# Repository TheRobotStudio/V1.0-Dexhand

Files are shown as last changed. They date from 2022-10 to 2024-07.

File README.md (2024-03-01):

# V1.0-Dexhand

As a naming convention the forearm parts consist of a bulk, a split, inserts and shells - the stl files are in the Forearm folder.

The bulk is typically the larger of the forearm prints and houses the servos and other components.

The split is typically smaller and is effectively a lid though may also incorporate structural supports for components and other print inserts inside the forearm.

Inserts are detachable pieces necessary to assemble pieces inside the structure beneath other components.

Shells are thin coverings that cover over openings in the main structure.

Print all the files in the Forearm folder to make the forearm. The battery cover is optional and in practice the bulk shell seals all the components adequately if well printed.

Some minor updates still required to finalise the tendon routing in the forearm and hand.

There are two main forearm structure files, Bulk and Split and additionally two shells, one to cover the servos in the palm and a pair to cover the outside of the forearm and seal over the electronics and battery compartment.

The Split print has mounting holes for the battery springs and an external hole to mount a 16mm latching push button switch to turn the hand on and off.

To download the stl files click the green button above on the right to drop down the Code menu. At the bottom click Download Zip.

The hand is made entirely by 3dprinting with additional total cost of components required for the hand around $300 USD.

The cad for the arm and hand is freely and publically available down to a parasolid level at:

https://cad.onshape.com/documents/16c809d35214bd31c5b0324f/w/56b2fb82f7bdce505771766f/e/df78e66574dc7dbd45e4826c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

The forearm and hand can operate as a stand-alone unit allowing unlimited axial rotation for rotational tasks like scrubbing.

Some notes on printing:

The parts can be printed on any extrusion printer and the hand uses less than 300 USD of components.

The parasolid CAD model can also be viewed and downloaded for free on the cloud platform Onshape: https://cad.onshape.com/documents/16c809d35214bd31c5b0324f/w/56b2fb82f7bdce505771766f/e/df78e66574dc7dbd45e4826c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

Designed and tested for high speed printing using a 0.6mm diameter nozzle and 0.4mm layer thickness except for the tendon spools which benefit from printing at 0.3mm layer thickness or better.

Tested in PLA, PETG and CF nylon. ABS is not recommended for the large pieces due to warping.

To finish 3d prints to a high standard requires a fine sandpaper or emery board.

Diamond coated steel nail files are a handy tool: https://amzn.to/3VBBsOX

Though my favourite diamond file is actually intended for maintaining whetstones, just a nice big expanse of diamond dust to use :-)

- Amazon US: https://amzn.to/3eN3bvo

Additional components required are listed below.

Please consider buying via the Amazon links where available to help fund the robot development.

The biggest cost item are the 16 slim micro-servos that drive the fingers and thumb.

The discount code ROBOTSERVOS will take off 10% from the official Emax webstore: https://emaxmodel.com

There are four variants at this size with plastic or metal gears and using either digital or analog control technology.

ES3301 (approx $6.6)
ES3302 (approx $9.2)
ES3351  (approx $8.5)
ES3352 (approx $12)

2 standard micro servos are needed for wrist flexion and extension.

Feetech SCS2332 - https://feetechrc.com/product-name_55300.html are recommended.

These are serial bus driven servos over allowing a greater range of controlled rotation.

They cost around 35 bucks each plus delivery.

If you prefer to use a standard PWM servo for simplicity they can be substituted by any servo that fits inside the envelope 23.2*12.1*28.5mm.

The trade off is the reduction of the powered range of motion of the wrist to about half.

1 standard servo needed for axial wrist rotation (optional)
Feetech SCS15 - https://feetechrc.com/6v-15kg-digital-robot-steering-gear.html or any servo that fits inside the envelope 40*20*40.5mm.

Reduces powered range of motion to about half and the loss of a continuous rotation option.

The rest of the components are relatively inexpensive:

2mm diameter steel pins - alternatively cut lengths from a wire coat hanger or in Europe order direct from https://www.visseriefixations.fr/goupilles/goupille-cylindrique-rectifiee-m6.html

Otherwise kits are available on Amazon US: https://amzn.to/3VYrnfh

M2 screw and washer kits, or also in Europe from https://www.visseriefixations.fr
Amazon US: https://amzn.to/3sf4NkE

M2 brass threaded inserts M2 * 4mm long * 3.5mm
Note that the type required has a plain section between the knurled ends to allow attachment of the tendon in the fingertip.
Amazon US: https://amzn.to/3yYl1lY

Kite or fishing line for finger tendons - Sufix 832 is the best I know of for longevity, the 80lbs breaking strength is stiff enough to thread easily and most readily available on 
Amazon US: https://amzn.to/3DgjNoF

Slightly thicker 0.8mm kiteline for the finger ligaments and wrist tendons.

Amazon US: https://amzn.to/3GMKQJL

Ball Bearings 6*10*3 - Need 50 for a hand, packs of 10 available which are enough for the sample finger.
Amazon US: https://amzn.to/3Dj7cBn

Ball Bearings 2*6*3 or 2*6*2.5 - Need 6 for the wrist
Amazon US: https://amzn.to/3yYlTHg

Ball Bearings 15*21*4 - Need 4 for the wrist
Amazon US: https://amzn.to/3TsMSTO

Ball Bearings 3*8*4 - Need 6 for the wrist
Amazon US: https://amzn.to/3VyE28O

M3 * 70mm caphead bolt (grade 12.9 ideally)
Need 2 (1 is cut down to 60mm)
Amazon US: https://amzn.to/3HM0Rjx
McMaster US: https://www.mcmaster.com/product/91290A297

Follow @therobotstudio
Get involved at patreon.com/therobotstudio

Shield: [][cc-by-nc-sa]

This work is licensed under a
[Creative Commons Attribution-NonCommercial-ShareAlike 4.0 International License][cc-by-nc-sa].

[][cc-by-nc-sa]

[cc-by-nc-sa]: http://creativecommons.org/licenses/by-nc-sa/4.0/
[cc-by-nc-sa-image]: https://licensebuttons.net/l/by-nc-sa/4.0/88x31.png
[cc-by-nc-sa-shield]: https://img.shields.io/badge/License-CC%20BY--NC--SA%204.0-lightgrey.svg

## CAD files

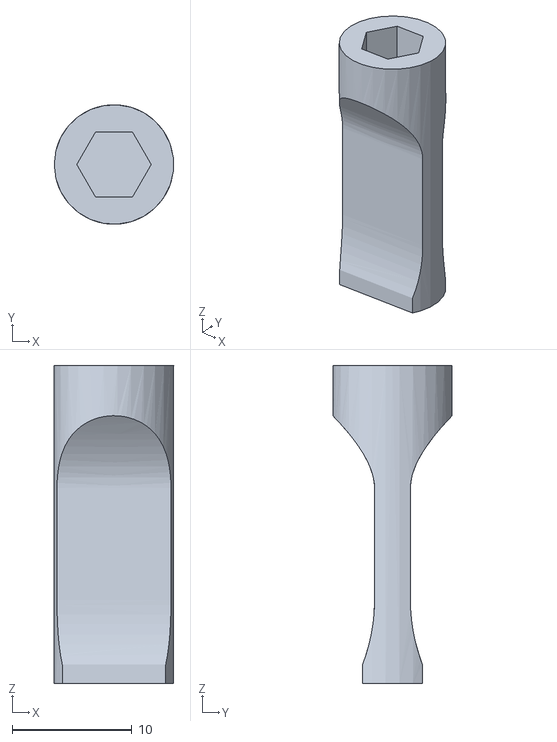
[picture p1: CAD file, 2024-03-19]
Forearm/M3_Socket_02.STL
10.0 x 10.00 x 26.6

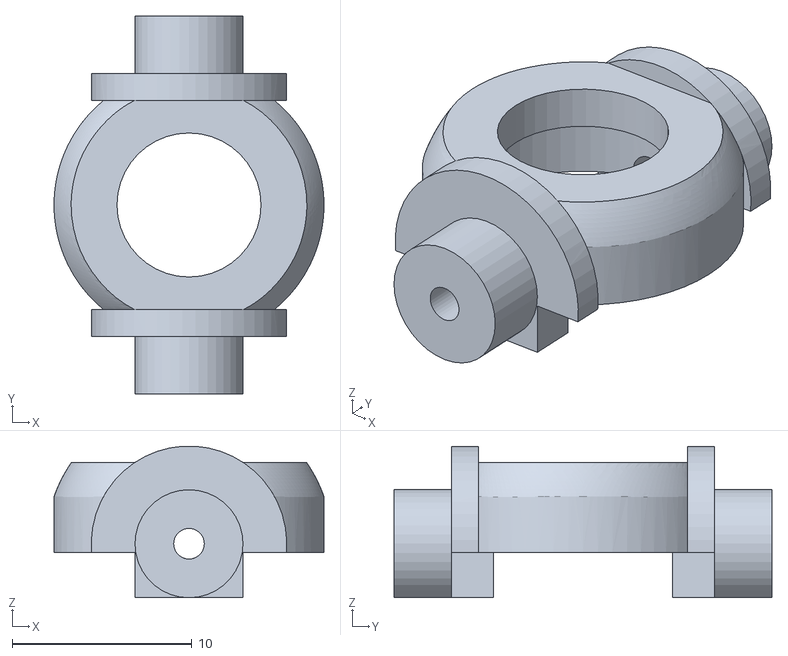
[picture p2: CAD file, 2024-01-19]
Hand_06/CMC_Yaw_15a.STL
15.0 x 21.0 x 8.42

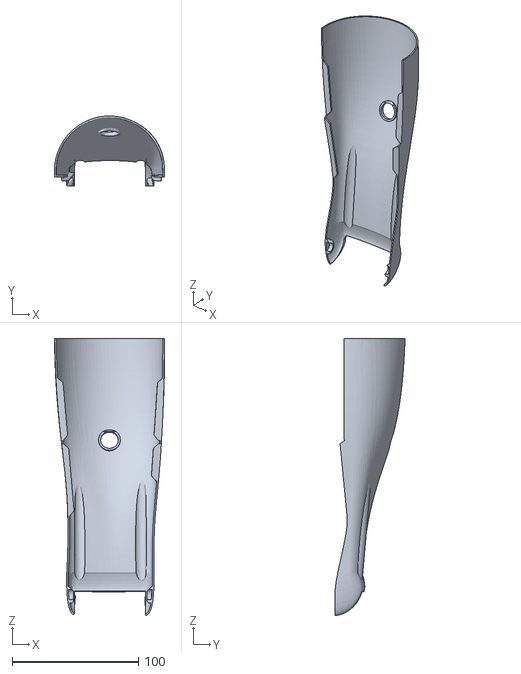
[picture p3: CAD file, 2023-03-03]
Patreon_Forearm_Shells/Forearm_Duplex_Wrist_19c_Jessie_02_Left_Split_Cover.STL
87.4 x 55.6 x 219.6

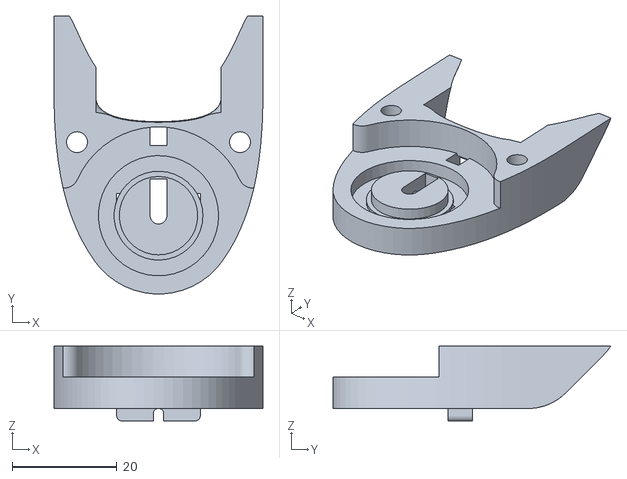
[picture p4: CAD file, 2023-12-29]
Wrist_10/Proximal_Wrist_10a_5mm_Holes.STL
40.0 x 53.2 x 14.4

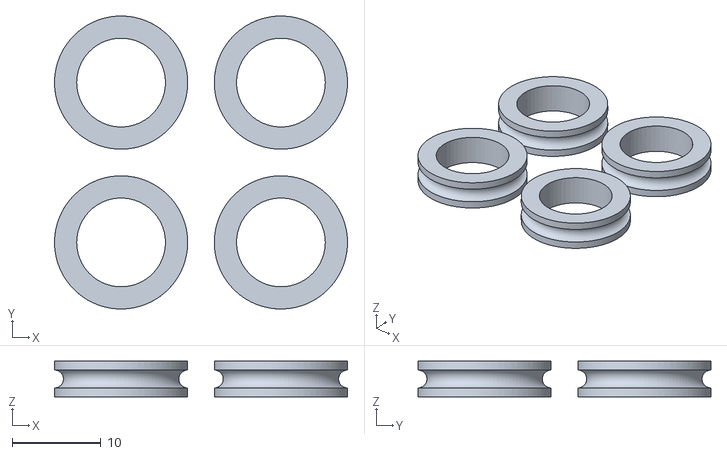
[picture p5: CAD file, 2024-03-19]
Forearm/10_15_4.STL
33.0 x 33.0 x 4.00

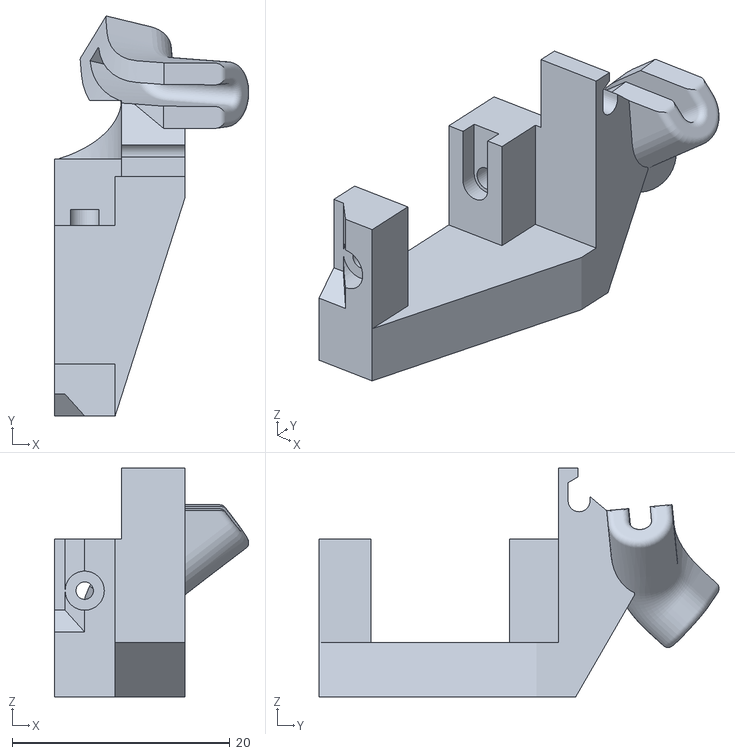
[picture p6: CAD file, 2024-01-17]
Hand_06/Thumb_Tendon_Hanger_03a.STL
17.9 x 36.8 x 21.0

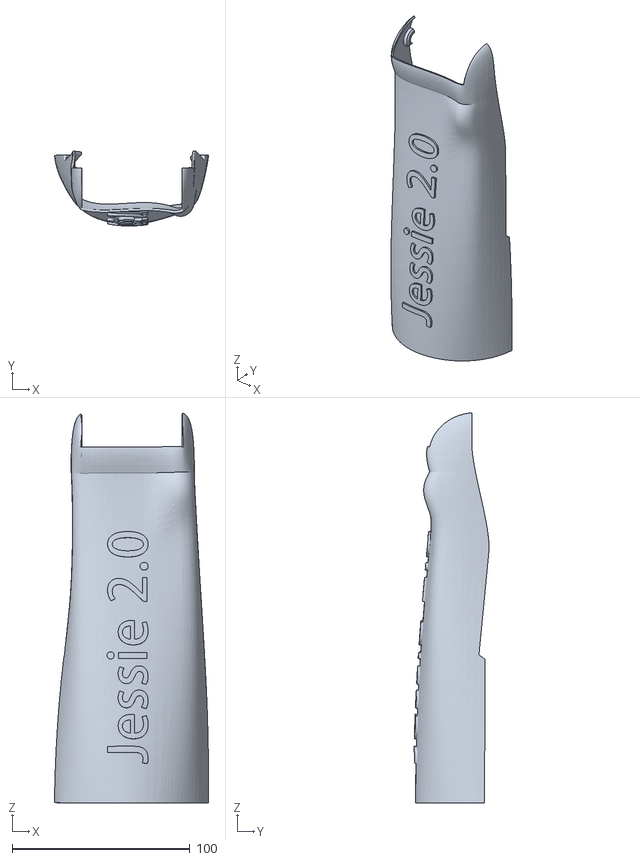
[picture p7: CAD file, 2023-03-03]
Patreon_Forearm_Shells/Forearm_Duplex_Wrist_19c_Jessie_02_Right_Bulk_Cover.STL
86.9 x 42.3 x 219.7

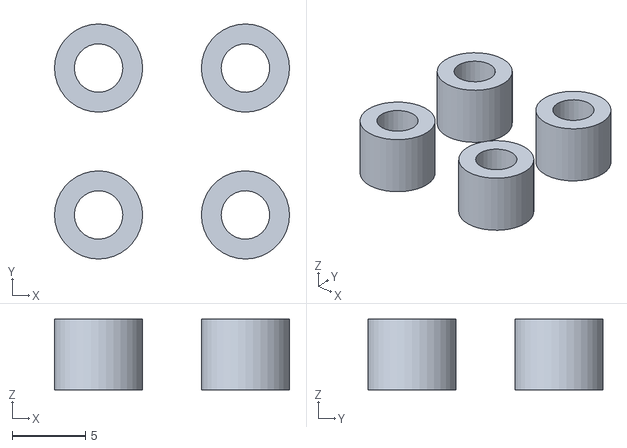
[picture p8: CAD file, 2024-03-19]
Forearm/Wrist_Pulley_Centres_03.STL
16.0 x 16.0 x 4.80

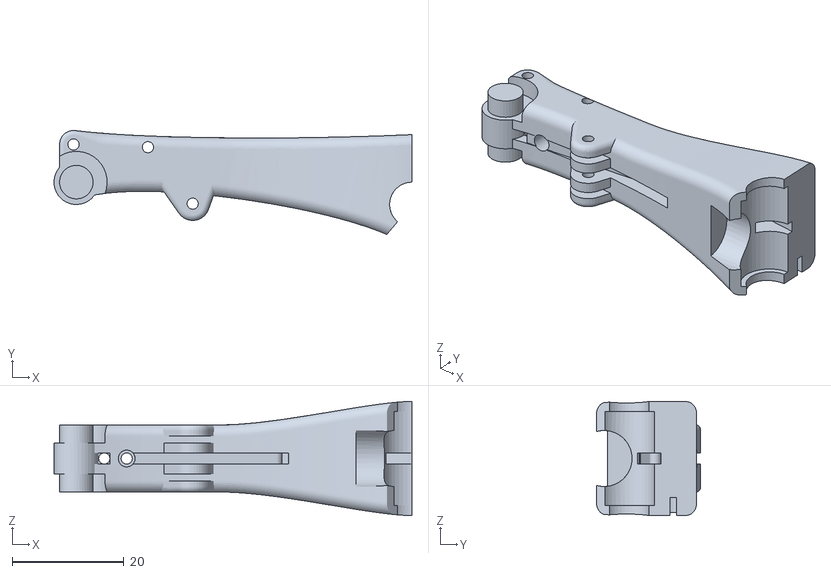
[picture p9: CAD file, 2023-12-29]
Hand_06/PLP_THUMB_15b.STL
64.0 x 18.6 x 20.4

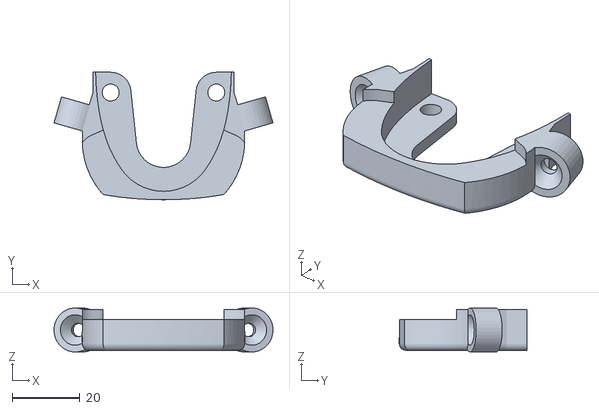
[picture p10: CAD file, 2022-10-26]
Wrist_10/Proximal_Wrist_10_Tendon_Hanger_5mm_Holes.STL
64.7 x 37.7 x 13.0

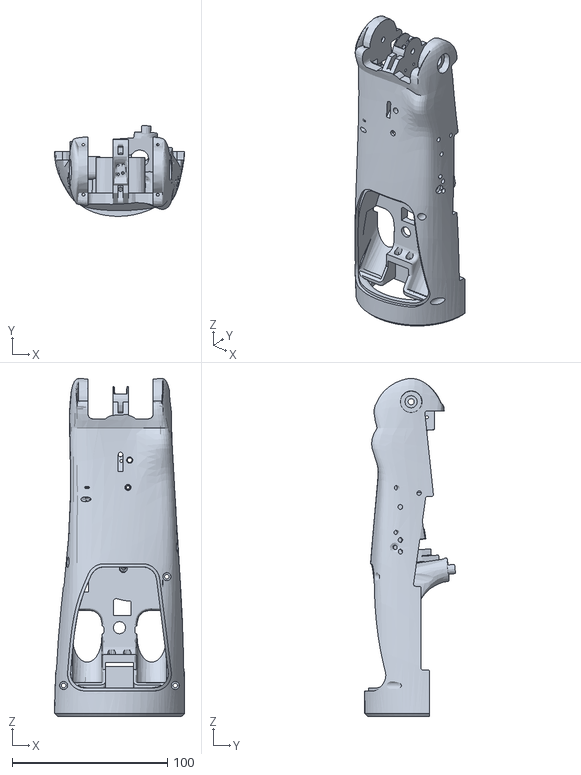
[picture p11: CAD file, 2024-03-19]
Forearm/Forearm_Duplex_Wrist_17j_Bulk.STL
84.0 x 58.5 x 218.0

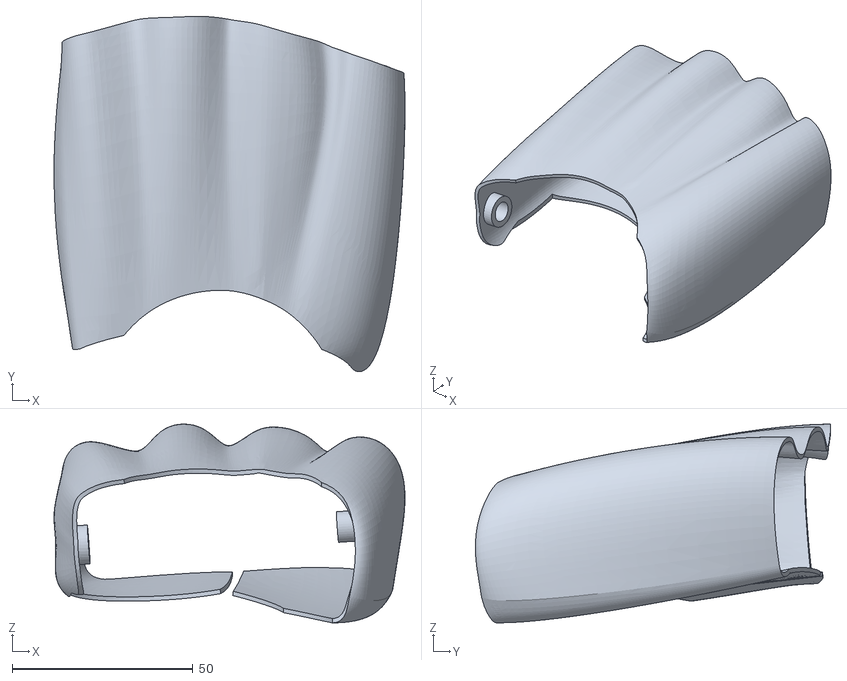
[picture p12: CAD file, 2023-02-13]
Hand_06/Back_of_Hand_23a.STL
97.1 x 98.3 x 55.0

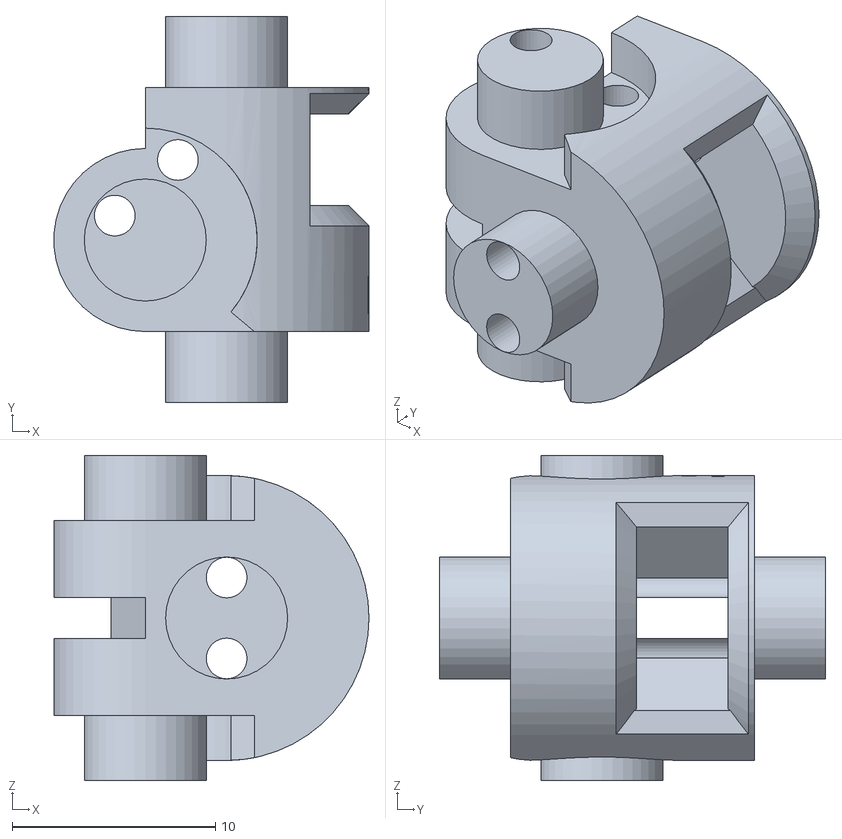
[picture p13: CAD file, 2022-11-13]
Hand_06/Knuckle_15.STL
15.5 x 19.0 x 16.0

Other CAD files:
Wrist_10/Proximal_Wrist_10a_4mm_Holes.STL
Patreon_Forearm_Shells/Forearm_Duplex_Wrist_19c_Jessie_02_Left_Bulk_Cover.STL
Patreon_Forearm_Shells/Forearm_Duplex_Wrist_19c_Jessie_02_Right_Split_Cover.STL
Wrist_10/Proximal_Wrist_10_Tendon_Hanger_4mm_Holes.STL
Forearm/Forearm_Duplex_Wrist_19c_TRS_01_Split_Cover.STL
Forearm/Forearm_Duplex_Wrist_18c_Insert_01.STL
Forearm/Forearm_Duplex_Wrist_18c_Insert_02.STL
Forearm/Forearm_Duplex_Wrist_18c_Insert_03.STL
Forearm/Forearm_Duplex_Wrist_18d_Battery_Cover.STL
Forearm/Forearm_Duplex_Wrist_18i_Split_a.STL
Forearm/Forearm_Duplex_Wrist_19c_TRS_01_Bulk_Cover.STL
Hand_06/CMC_Pitch_15.STL
Hand_06/MLP_100_15.STL
Hand_06/MLP_105_15.STL
Hand_06/MLP_90_15.STL
Hand_06/MLP_THUMB_15.STL
Hand_06/PLP_100_15.STL
Hand_06/PLP_105_15.STL
Hand_06/PLP_90_15.STL
Hand_06/Palm_Fore_Bulk_15.STL
Hand_06/Palm_Fore_Split_15.STL
Hand_06/Palm_Little_Bulk_15.STL
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

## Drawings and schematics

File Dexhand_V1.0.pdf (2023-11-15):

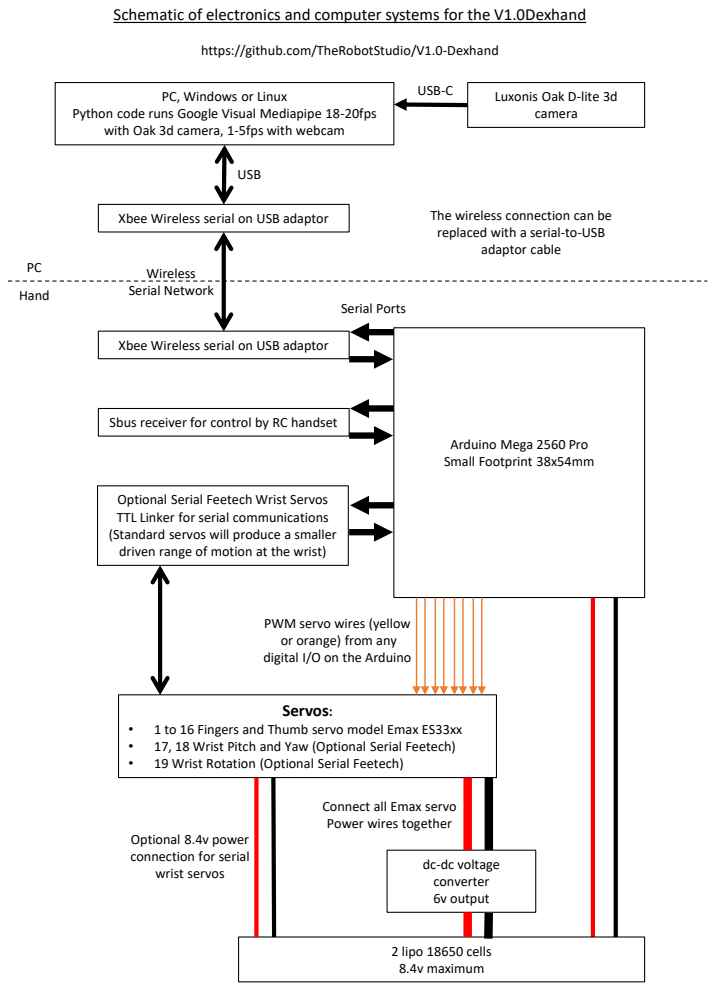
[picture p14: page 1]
Servos:; USB; Wireless Serial Network; Serial Ports; adaptor cable; USB-C; 2 lipo 18650 cells 8.4v maximum; Hand

Schematic of electronics and computer systems for the V1.0Dexhand

https://github.com/TheRobotStudio/V1.0-Dexhand

PC, Windows or Linux

Luxonis Oak D-lite 3d
camera

Python code runs Google Visual Mediapipe 18-20fps
with Oak 3d camera, 1-5fps with webcam

The wireless connection can be
replaced with a serial-to-USB

Xbee Wireless serial on USB adaptor

Sbus receiver for control by RC handset

Arduino Mega 2560 Pro
Small Footprint 38x54mm

Optional Serial Feetech Wrist Servos
TTL Linker for serial communications
(Standard servos will produce a smaller
driven range of motion at the wrist)

PWM servo wires (yellow
or orange) from any
digital I/O on the Arduino

• 1 to 16 Fingers and Thumb servo model Emax ES33xx
• 17, 18 Wrist Pitch and Yaw (Optional Serial Feetech)
• 19 Wrist Rotation (Optional Serial Feetech)

Connect all Emax servo
Power wires together

Optional 8.4v power
connection for serial
wrist servos

dc-dc voltage
converter
6v output

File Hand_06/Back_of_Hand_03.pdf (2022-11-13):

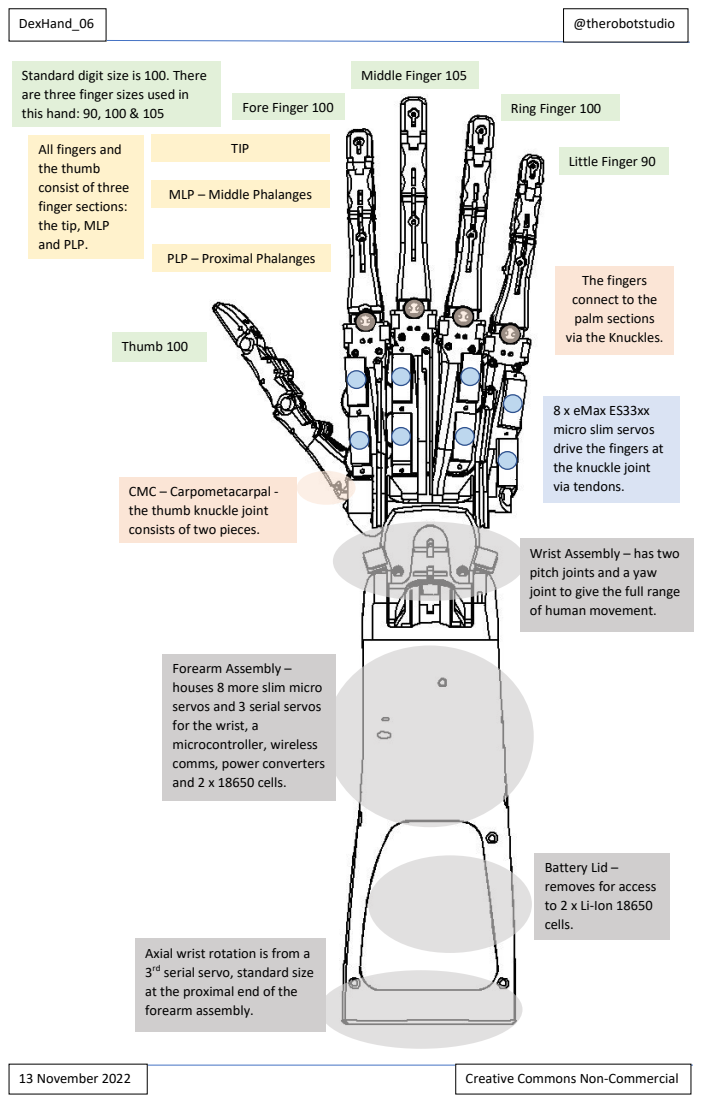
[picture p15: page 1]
DexHand_06; @therobotstudio; 13 November 2022; Creative Commons Non-Commercial; Little Finger 90; Ring Finger 100; Middle Finger 105; Fore Finger 100; Thumb 100; TIP

Standard digit size is 100. There
are three finger sizes used in
this hand: 90, 100 & 105

All fingers and
the thumb
consist of three
finger sections:
the tip, MLP
and PLP.

MLP – Middle Phalanges

PLP – Proximal Phalanges

The fingers
connect to the
palm sections
via the Knuckles.

8 x eMax ES33xx
micro slim servos
drive the fingers at
the knuckle joint

via tendons. CMC – Carpometacarpal -

the thumb knuckle joint consists of two pieces.

Wrist Assembly – has two pitch joints and a yaw joint to give the full range of human movement.

Forearm Assembly –
houses 8 more slim micro
servos and 3 serial servos
for the wrist, a
microcontroller, wireless
comms, power converters
and 2 x 18650 cells.

Battery Lid – removes for access to 2 x Li-Ion 18650 cells.

Axial wrist rotation is from a 3 rd serial servo, standard size at the proximal end of the forearm assembly.

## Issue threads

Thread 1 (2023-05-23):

BOM - Missing Some Bearing Sizes

tshumay, 2023-05-23:
Reminder to add bearing sizes for the bearings that go between the 70mm M3 Bolt and Bulks.

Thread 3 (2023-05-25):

BOM - Mating Connector for M3 Countersunk Screws in Wrist

tshumay, 2023-05-25:
Currently unclear what kind of flush connector to use for M3 countersunk screws - heat sink? Sleeve nut?

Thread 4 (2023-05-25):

Geometry - Thumb heat-sink insert not in right place.

tshumay, 2023-05-25:
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

I believe this bore may be in the wrong place if it is intended to accept the heat-set insert from the top of the thumb

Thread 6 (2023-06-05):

Unclear Which Shells Fit Together

tshumay, 2023-06-05:
I'm not sure if there's a matching top/bottom shell set in the STL files. I printed the Forearm_Duplex_Wrist17f_Bulk forearm as my basis, but none of the top shells seem to fit. I started with Forearm_Duplex_Wrist_18i_Split, but there is a gap. And the others seem to not fit  in CAD.

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

TheRobotStudio, 2023-06-06:
Yes that’s right, the gap allows the cosmetic shells to clip on!On the V2 it’s neater 😁Sent from my iPhoneOn 5 Jun 2023, at 22:43, Trent Shumay ***@***.***> wrote:
I'm not sure if there's a matching top/bottom shell set in the STL files. I printed the Forearm_Duplex_Wrist17f_Bulk forearm as my basis, but none of the top shells seem to fit. I started with Forearm_Duplex_Wrist_18i_Split, but there is a gap. And the others seem to not fit  in CAD.

—Reply to this email directly, view it on GitHub, or unsubscribe.You are receiving this because you are subscribed to this thread.Message ID: ***@***.***>

tshumay, 2023-06-06:
Ahhh! That makes sense. Thanks! I’ve got the right ones printed then. _____________________________Trenton ShumayCEO, IoT Design Shop Inc. On Jun 5, 2023, at 9:57 PM, TRS ***@***.***> wrote:
Yes that’s right, the gap allows the cosmetic shells to clip on!On the V2 it’s neater 😁Sent from my iPhoneOn 5 Jun 2023, at 22:43, Trent Shumay ***@***.***> wrote:
I'm not sure if there's a matching top/bottom shell set in the STL files. I printed the Forearm_Duplex_Wrist17f_Bulk forearm as my basis, but none of the top shells seem to fit. I started with Forearm_Duplex_Wrist_18i_Split, but there is a gap. And the others seem to not fit  in CAD.

—Reply to this email directly, view it on GitHub, or unsubscribe.You are receiving this because you are subscribed to this thread.Message ID: ***@***.***>

—Reply to this email directly, view it on GitHub, or unsubscribe.You are receiving this because you authored the thread.Message ID: ***@***.***>

Closed 2023-06-07.

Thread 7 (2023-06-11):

Geometry - Mechanical Interference

tshumay, 2023-06-11:
Especially with some deviation in 3D printing, there is a mechanical interference with the top right tendon port and the servo mounting positions on the forearm.

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

TheRobotStudio, 2023-07-23:
Yes - this is intended to be cleared with a 2mm drill prior to assembly!

tshumay, 2023-07-23:
It's not the hole itself, so much as the tendon being impeded by the servo body. I cleared the holes, but it's obscured by the mount tail of the servo.

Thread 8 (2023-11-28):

SG90 Alternative Micro Servo Model

ingochris, 2023-11-28:
```
Future iterations will be able to fit SC90 servos which are considerably cheaper.
```

Saw this on another platform (thing:5466653) but comments aren't pushing there for some reason.
I'm guessing your team meant SG90 micro servos.

My question is:
Was this ever integrated to the STL's and microcontroller code?

TheRobotStudio, 2023-11-28:
Hi,

I've yet to finish modifying the stl's but the code would be the same as SG90's and Emax ES33xx servos are both legacy PWM servos.

Cheers,

Rob

ingochris, 2023-11-29:
Thanks, looking forward to it! I have printer and SG90's ready to test once the model is updated.

TheRobotStudio, 2023-11-29:
There is a single finger example of you want to try now: https://www.thingiverse.com/thing:5384399Sent from my iPhoneOn 29 Nov 2023, at 02:50, Christopher Ngo ***@***.***> wrote:
Thanks, looking forward to it! I have printer and SG90's ready to test once the model is updated.

—Reply to this email directly, view it on GitHub, or unsubscribe.You are receiving this because you commented.Message ID: ***@***.***>

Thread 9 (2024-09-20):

1 finger fill missing

jahid0298, 2024-09-20:
I can see here 4 finger. One is missing

TheRobotStudio, 2024-09-21:
There are three fingers specified in the stl because the 1st finger and the 3rd finger are identical. The middle finger is 105% relative size and the little finger is 90%.

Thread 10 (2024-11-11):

Steering gear power supply

dadffaser, 2024-11-11:
I would like to know how the ten motors of the dexhand are controlled, how do you solve the power supply problem of so many motors

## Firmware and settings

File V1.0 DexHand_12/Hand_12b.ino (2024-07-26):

/*   Copyright 2021 Feetech RC Model CO.,LTD
 *
 *  Licensed under the Apache License, Version 2.0 (the "License");
 *  you may not use this file except in compliance with the License.
 *  You may obtain a copy of the License at
 *
 *       http://www.apache.org/licenses/LICENSE-2.0
 *
 *  Unless required by applicable law or agreed to in writing, software
 *  distributed under the License is distributed on an "AS IS" BASIS,
 *  WITHOUT WARRANTIES OR CONDITIONS OF ANY KIND, either express or implied.
 *  See the License for the specific language governing permissions and
 *  limitations under the License.

 Compared to Hand_12 the function of the serial ports 0 and 3 have been swapped over.
 This means that now the servos can be controlled without an additional USB to serial connection from the PC.
 The standard USB connection built into the Arduino mega will now read serial output from the PC.
 If an extra FTDI or CH340 USB to serial adaptor is available it can be connected to serial port 3 for debugging.

 On the mega Pin 14 is TxD connects to Yellow (FTDI) or White (CH340)
             Pin 15 is RxD connects to Orange (FTDI) or Green (CH340)

 For both types Red connects to +5v
                Black connects to Ground           

 */

 
#include "SBUS.h"
#include "Servo.h"
#include "SCServo.h"

// a SBUS object, which is on hardware
// serial port 1
SBUS x8r(Serial1);

Servo emaxservo_RTI;  // 26 RT I Ring Tendon Inverted, 27, 28, 29, 30, 31, 24, 48, 49, 50, 51, 52, 53, 45, 46, 47
Servo emaxservo_LTI;  // 27 LT I Little Tendon Inverted
Servo emaxservo_LON;  // 28 LO N Little Outward at Knuckle Non-Inverted
Servo emaxservo_LII;  // 29 LI I Little Inward at Knuckle Inverted
Servo emaxservo_ROI;  // 30 RO I Ring Outward
Servo emaxservo_RII;  // 31 RI Ring Inward
Servo emaxservo_TRN;  // 24 TR N Thumb Rotation Non-Inverted
Servo emaxservo_FTN;  // 48 FT N Fore Tendon Non
Servo emaxservo_MTN;  // 49 MT N Middle Tendon Non
Servo emaxservo_FII;  // 51 FI I Fore Inward Inverted
Servo emaxservo_FON;  // 50 FO N
Servo emaxservo_MON;  // 52 MO N
Servo emaxservo_MIN;  // 53 MI N
Servo emaxservo_TII;  // 45 TI I Thumb Inwards
Servo emaxservo_TTN;  // 46 TT N Thumb Tendon Non
Servo emaxservo_TON;  // 47 TO N Thumb Outwards Non



// twelve servo objects can be created on most boards.
//On the Mega, up to 12 servos can be used without interfering with PWM functionality; use of 12 to 23 motors will disable PWM on pins 11 and 12.

int pos[] ={0, 0, 0, 0,
            0, 0, 0, 0,
            0, 0, 0, 0,
            0, 0, 0, 0};    // variable to store positions


int servo_pos[] ={90, 90, 90, 90,       // variable to store the servo positions for four fingers (3 powered dof each) and thumb (4 powered dof)
                  90, 90, 90, 90,       // setting to zero causes little servo jump at start up
                  90, 90, 90, 90,
                  90, 90, 90, 90}; 

int wrist_pos[] = {512, 512, 512};     // default to centre

// channel, fail safe, and lost frames data
uint16_t channels[16];
bool failSafe;
bool lostFrame;

long default_counter = 1;
int default_stage = 0;


SCServo SERVO;      //Declare a case of SCServo to control the Feetechs

//
int analogPin0 = A0; // potentiometer wiper (middle terminal) connected to analog pin 0
                    // outside leads to ground and +5V
int analogPin1 = A1;  //Knuckle Yaw
int analogPin2 = A2;  //Sequence
                    
int val0 = 0;  // variable to store the value read
int val1 = 0;
int val2 = 0;
int a = 0;      //Print out angles
int b = 0;      //Servo limits for loop
int l = 0;      //for loop counter
int s = 511;      //sequence counter
bool Sense = 1;

int bytecount = 0;
int bus_start = 0;
int bus_end = 0;
int checksum = 0;
int angles[23] = {0};
byte lo;            //low byte of checksum int

int digi = 0;
int digitemp = 0;
int newmsg = 0;

int action = 0;
int prev_action = 0;

int ring_offset = 0;

//White Hand
//ID1: 380 570
//ID2: 0 1023
//ID3: 360 570
//ID4: 0 1023
//ID5: 450 640
//ID6: 0 1023 Neg
//ID7: 40 600
//ID8: 0 1023 Neg
//ID9: 400 800 Neg
//ID10: 0 1023
int Servo_Min[] = {0, 380, 0, 360, 0, 450, 0, 400, 0, 400, 0};
int Servo_Max[]= {0, 570, 1023, 570, 1023, 640, 1023, 600, 1023, 800, 1023};
int Mid_Point[10];

int wrist[2] = {512, 512};
int Servo_Order[]= {26, 27, 28, 29, 
                    30, 31, 24, 48,
                    49, 50, 51, 52,
                    53, 45, 46, 47};

void setup() {
  //The Mega and Due boards have 4 UART each
  //For the Mega  RX0 = D0, TX0 = D1
  //              RX1 = D19, TX1 = D18
  //              RX2 = D17, TX2 = D16
  //              RX3 = D15, TX3 = D14

  
  Serial.begin(115200);       //Comms with PC
  Serial.print("Connected on Serial\n\r");
  Serial.print("File   : "), Serial.println(__FILE__);
  Serial.print("Date   : "), Serial.println(__DATE__);

  //Serial.print("Connected on Serial0\n\r");

  Serial3.begin(115200);      //Comms with FTDI or CH340 USB to serial adaptor
  Serial3.print("Connected on Serial3\n\r");
  Serial3.print("File   : "), Serial3.println(__FILE__);
  Serial3.print("Date   : "), Serial3.println(__DATE__);


  x8r.begin();                          // begin the SBUS communication on Serial1
  // x8r.begin(22, 23, false, 100000); // optional parameters for ESP32: RX pin, TX pin, inverse mode, baudrate
  
  Serial2.begin(1000000);     //Comms with Feetech servos RX2 = D17, TX2 = D16                                                                                                                                                                                                                                                                                                                                                                                                                                                                                                                                                                                                                                                                                                                                                                                                                                                                                                                                                                                                                                                                                                                                                                                                                                                                                                                                                                                                                                                                                                                                                                                                                                                                                                                                                                                                                                                                                                                          
  SERVO.pSerial = &Serial2;

  emaxservo_FON.attach(50);  // 50 FO N Fore Outwards Normal
  emaxservo_FII.attach(51);  // 51 FI I Fore Inward Inverted
  emaxservo_FTN.attach(48);  // 48 FT N Fore Tendon Non
   
  emaxservo_MON.attach(52);  // 52 MO N Middle Outwards Normal
  emaxservo_MIN.attach(53);  // 53 MI N Middle Inwards Normal
  emaxservo_MTN.attach(49);  // 49 MT N Middle Tendon Non
  
  emaxservo_ROI.attach(30);  // 30 RO I Ring Outward Inverted
  emaxservo_RII.attach(31);  // 31 RI I Ring Inward Inverted 
  emaxservo_RTI.attach(26);  // 26 RT I Ring Tendon Inverted
  
  emaxservo_LON.attach(28);  // 28 LO N Little Outward at Knuckle Non-Inverted
  emaxservo_LII.attach(29);  // 29 LI I Little Inward at Knuckle Inverted
  emaxservo_LTI.attach(27);  // 27 LT I Little Tendon Inverted
  
  emaxservo_TON.attach(47);  // 47 TO N Thumb Outwards Non
  emaxservo_TII.attach(45);  // 45 TI I Thumb Inwards Inverted
  emaxservo_TTN.attach(46);  // 46 TT N Thumb Tendon Non
  emaxservo_TRN.attach(24);  // 24 TR N Thumb Rotation Non-Inverted
 
  
  delay(50);                 //Try shorter than 500
}

void loop()
{
      //Serial3.print("Loop ");
      

  // For an SBUS type controller. First look for a good SBUS packet from the receiver, has dominance over Xbee signal
  if(x8r.read(&channels[0], &failSafe, &lostFrame))
  {

    // write the SBUS packet to an SBUS compatible servo
    //x8r.write(&channels[0]);
   
    for(int i=0; i<16; i++){ 
     //Serial3.print(channels[0], DEC);
      Serial3.print(i+1, DEC);
      Serial3.print(" ");
      Serial3.print(channels[i], DEC);   //For reasons that are unclear Channel 16 is not stable. The others seem solid. Signal swings 172 to 1811
    
     if(i==15){
         Serial3.print(" \n\r");
     }
     else{
        Serial3.print("  ");
      } 
    }
    /*
    for(int i=0; i<16; i++){
      pos[i] = map(channels[0], 172, 1811, 0, 180);
    }

    // tell servo to go to position in variable 'pos' varies from 0 to 180 degrees
    
    emaxservo_01.write(pos[0]);
    emaxservo_02.write(pos[1]);
    emaxservo_03.write(pos[2]);
    emaxservo_04.write(pos[3]);
    emaxservo_05.write(pos[4]);
    emaxservo_06.write(pos[5]);
    emaxservo_07.write(pos[6]);
    emaxservo_08.write(pos[7]);
    emaxservo_09.write(pos[8]);
    emaxservo_10.write(pos[9]);
    emaxservo_11.write(pos[10]);
    emaxservo_12.write(pos[11]);
    emaxservo_13.write(pos[12]);
    emaxservo_14.write(pos[13]);
    emaxservo_15.write(pos[14]);
    emaxservo_16.write(pos[14]);    //Due to protocol instability in Channel 16
    */
    //Use Switch SE as it's the only one listed for unknown reasons
    //Goes to plus or minus 100%
    //Away is minus

    if(channels[4] < 200)     //all move together
    {    
      pos[0] = map(channels[0], 172, 1811, 30, 150);      //Tendon
      pos[1] = map(channels[0], 172, 1811, 150, 30);      //Tendon Inverted
      pos[2] = map(channels[1], 172, 1811, 30, 150);      //Outward InterRos
      pos[3] = map(channels[1], 172, 1811, 150, 30);      //Inverted
      pos[4] = map(channels[2], 172, 1811, 30, 150);      //Inward InterRos
      pos[5] = map(channels[2], 172, 1811, 150, 30);      //Inverted

      pos[6] = map(channels[3], 172, 1811, 160, 40);      //Thumb rotation
      
      emaxservo_FTN.write(pos[0]);  // 48 FT N Fore Tendon Non
      emaxservo_MTN.write(pos[0]);  // 49 MT N Middle Tendon Non
      emaxservo_RTI.write(pos[1]);  // 26 RT I Ring Tendon Inverted, 27, 28, 29, 30, 31, 24, 48, 49, 50, 51, 52, 53, 45, 46, 47
      emaxservo_LTI.write(pos[1]);   // 27 LT I Little Tendon Inverted
      
      emaxservo_FON.write(pos[2]);  // 51 FO N Fore Outward Normal
      emaxservo_MON.write(pos[2]);  // 52 MO N Middle Outward Normal
      emaxservo_ROI.write(pos[3]);  // 30 RO I Ring Outward Inverted
      emaxservo_LON.write(pos[2]);  // 28 LO N Little Outward at Knuckle Non-Inverted
      
      emaxservo_FII.write(pos[5]);  // 50 FI I Fore Inward Inverted
      emaxservo_MIN.write(pos[4]);  // 53 MI N Middle Inwards Normal
      emaxservo_RII.write(pos[5]);  // 31 RI I Ring Inward Inverted
      emaxservo_LII.write(pos[5]);  // 29 LI I Little Inward at Knuckle Inverted
      
      emaxservo_TTN.write(pos[0]);  // 46 TT N Thumb Tendon Non
      emaxservo_TON.write(pos[2]); // 47 TO N Thumb Outwards Non
      emaxservo_TII.write(pos[5]);  // 45 TI I Thumb Inwards
      
      emaxservo_TRN.write(pos[6]); // 24 TR N Thumb Rotation Non-Inverted

      pos[7] = map(channels[1], 172, 1811, 0, 1024);      //Wrist
      pos[8] = map(channels[2], 172, 1811, 0, 1024);      //Wrist
      pos[9] = map(channels[3], 172, 1811, 0, 1024);      //Wrist

      Serial3.print("Wrist\n\r");
      SERVO.WritePos(1, pos[7], 500);
      SERVO.WritePos(2, pos[8], 500);
      SERVO.WritePos(3, pos[9], 200);
    }
    else      //Turn off wrist
    {
      pos[0] = map(channels[0], 172, 1811, 30, 150);      //Tendon
      pos[1] = map(channels[0], 172, 1811, 150, 30);      //Tendon Inverted
      pos[2] = map(channels[1], 172, 1811, 30, 150);      //Outward InterRos
      pos[3] = map(channels[1], 172, 1811, 150, 30);      //Inverted
      pos[4] = map(channels[2], 172, 1811, 30, 150);      //Inward InterRos
      pos[5] = map(channels[2], 172, 1811, 150, 30);      //Inverted

      pos[6] = map(channels[3], 172, 1811, 160, 40);      //Thumb rotation
      pos[10] = map(channels[0], 172, 1811, 30, 100);      //Tendon
      
      
      emaxservo_FTN.write(pos[0]);  // 48 FT N Fore Tendon Non
      emaxservo_MTN.write(pos[0]);  // 49 MT N Middle Tendon Non
      emaxservo_RTI.write(pos[1]);  // 26 RT I Ring Tendon Inverted, 27, 28, 29, 30, 31, 24, 48, 49, 50, 51, 52, 53, 45, 46, 47
      emaxservo_LTI.write(pos[1]);   // 27 LT I Little Tendon Inverted
      
      emaxservo_FON.write(pos[5]);  // 51 FO N Fore Outwards Normal
      emaxservo_MON.write(pos[2]);  // 52 MO N Middle Outwards Normal
      emaxservo_ROI.write(pos[3]);  // 30 RO I Ring Outward Inverted
      emaxservo_LON.write(pos[2]);  // 28 LO N Little Outward at Knuckle Non-Inverted
      
      emaxservo_FII.write(pos[2]);  // 50 FI I Fore Inward Inverted
      emaxservo_MIN.write(pos[4]);  // 53 MI N Middle Inwards Normal
      emaxservo_RII.write(pos[5]);  // 31 RI Ring Inward
      emaxservo_LII.write(pos[5]);  // 29 LI I Little Inward at Knuckle Inverted
      
      emaxservo_TTN.write(pos[10]);  // 46 TT N Thumb Tendon Non
      emaxservo_TON.write(pos[2]); // 47 TO N Thumb Outwards Non
      emaxservo_TII.write(pos[5]);  // 45 TI I Thumb Inwards

      emaxservo_TRN.write(pos[6]); // 24 TR N Thumb Rotation Non-Inverted   
    }

   }

  else if (Serial.available())       //Comms on serial0
  {
    default_counter = 1;              //Starts counter in event no Xbee signal received
    
    int inByte = Serial.read();          //read in the byte

    if(bytecount >= 0 )        bytecount++;                          //Increment once per loop

    //Debug to terminal
    //Serial3.print("\n\r");
    //Serial3.print("IN ");
    //Serial3.print(inByte, DEC);
    //Serial3.print(", ");
    //Serial3.print(" BC ");
    //Serial3.print(bytecount, DEC);
    //Serial3.print("\n\r");
    //Serial3.print(" ");         
  
    //read and decode the serial bus data cmoing over the xbee
    if(inByte == 0xFE && bytecount == 1)      //bytecount == 1, i.e. byte 1 - First 0xFE toggle flag
    {
        bus_start = 1;
        //Serial3.print("bus start \n\r");
        //Serial3.print(bytecount, DEC);
        //Serial3.print("    ");
        
    }
    else if(inByte == 0xFE && bytecount == -1)      //bytecount == -1, bus had to force restart
    {
        bus_start = 1;
        bytecount = 1;
        Serial3.print("bus force restart ");            
    }
    else if(inByte == 0xFE && bytecount == 2 && bus_start == 1)   //byte 2 - Two 0xFE received in a row - should not be possible to generate these angles
    {
        bus_start = 2;
        //Serial3.print("Start message   ");
    }
    else if(bytecount == 3 && bus_start == 2)             //3 First byte of data after start bytes so initialise
    {
        //Serial3.print(inByte);
        //Serial3.print("    ");
        //Serial3.println();
        angles[bytecount - 3] = inByte;
        checksum = inByte;
    }
    
    else if(bytecount >= 4 && bytecount <26) //load angles straight in
    {
        angles[bytecount - 3] = inByte;
        //Serial3.print(bytecount);
        checksum += inByte;
        
    }
    else if(bytecount == 26)             //byte  - CheckSum
    {
        checksum += inByte;
        //Serial3.print(checksum, BIN);
        lo = lowByte(checksum);
        //Serial3.print("bc %d  ", bytecount);
        //Serial3.print(" Check   ");
        //Serial3.print(lo);
        //Serial3.print(" \n\r");
    }
    else if(inByte == 0xFD && bytecount == 27 && lo == 255)             //byte 13 - Toggle end of bus flag
    {
        bus_end = 1;
        //Serial3.print("End byte 1");

    }
            
    else if(inByte == 0xFD && bytecount == 28 && bus_end == 1)             //byte 14 - Resets and toggle command received flag everything good
    {
        //reset bus
        bytecount = 0;
        checksum = 0;
        lo = 0;
        bus_end = 0;
        bus_start = 0;

        //Trigger servos. Each action must only issue once.
        action = 1;
        
        //Serial3.print("Message Received correctly \n\r");
        for(a=0; a<23; a++)
        {
          Serial3.print(angles[a]);
          Serial3.print("  ");
        }
        Serial3.print("\n\r");
        
        
        //Serial3.print(action);
        //Serial3.print(" \n\r");
    }
        
    else if(bytecount > 28)                                                 //End of message missed error
    {
        bytecount = -1;                                               //reset bytecount, etc so the cycle runs again when first byte 0xAA received
        checksum = 0;
        lo = 0;
        digitemp = 0;
        bus_end = 0;
        bus_start = 0;
        action = 0;

        Serial3.print("Serial bus error\n\r");
    }
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

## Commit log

2022-10-26 stl files for the forearm
    Version 18c of the stl files for the forearm section of the Dexhand
    [Forearm_Duplex_Wrist_18c_Battery_Lid.STL, Forearm_Duplex_Wrist_18c_Bulk.STL, Forearm_Duplex_Wrist_18c_Insert_01.STL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]
2023-02-13 The final stl's for the CES 2023 prototype
    Many small tweaks to the main forearm structure discovered through the assembly and commissioning process to produce a demonstration robot hand for CES 2023.
    Additonally two shells to improve the appearance of the hand and forearm:
    Back_of_Hand_23a.stl clips to the hand and covers all the servos in the palm.
    Forearm_Duplex_Wrist_19_Bling_Cover_02f.stl is a thin shell that covers the outside of the forearm and doubles as an alternative cover for the battery and electronics compartment. Additionally it can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
    [Back_of_Hand_23a.STL, Forearm_Duplex_Wrist_18i_Split_a.STL, Forearm_Duplex_Wrist_18j_Bulk.STL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]
2023-02-13 Add files via upload
    Battery cover with screw hole and front clip
    [Forearm_Duplex_Wrist_18d_Battery_Cover.STL]
2023-02-20 Right forearm shell
    [Forearm_Duplex_Wrist_19c_Jessie.STL]
2023-03-03 Complete covers for both forearms
    [Forearm_Duplex_Wrist_19c_Jessie_02_Left_Bulk_Cover.STL, Forearm_Duplex_Wrist_19c_Jessie_02_Left_Split_Cover.STL, Forearm_Duplex_Wrist_19c_Jessie_02_Right_Bulk_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]
2023-03-06 Bulk_17 version with clearance for the shells
    The outer aesthetic shells require a clearance for the retaining clips. In the version shown at CES 2023 this was created more or less by accident as the existing prototype had already been assembled with an earlier version - Forearm_Duplex_Wrist_17f_Bulk.STL
    [Forearm_Duplex_Wrist_17f_Bulk.STL]
2023-03-06 Delete Forearm_Duplex_Wrist_18j_Bulk.STL
    Removed to avoid confusion!
    [Forearm_Duplex_Wrist_18j_Bulk.STL]
2023-03-08 Delete Forearm_Duplex_Wrist_18c_Split.STL
    The mounting hole for the switch is missing
    [Forearm_Duplex_Wrist_18c_Split.STL]
2023-03-08 Add files via upload
    Later version of split with hole for switch
    [Forearm_Duplex_Wrist_18i_Split_a.STL]
2023-03-08 Add files via upload
    Battery lid with front clip
    [Forearm_Duplex_Wrist_18d_Battery_Cover.STL]
2023-03-08 All files now in single folder
    The cover is easier to use than the battery lid and allows for personalisation.
    [Forearm_Duplex_Wrist_18c_Insert_01.STL, Forearm_Duplex_Wrist_18c_Insert_02.STL, Forearm_Duplex_Wrist_18c_Insert_03.STL]
2023-03-08 Delete Forearm_18c directory
    All files now in Post CES 2023 folder.
    [Forearm_Duplex_Wrist_18c_Bulk.STL, Forearm_Duplex_Wrist_18c_Insert_01.STL, Forearm_Duplex_Wrist_18c_Insert_02.STL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]
2023-03-08 Delete Forearm_Duplex_Wrist_19_Bling_Cover_02f.STL
    Replaced by complete shell design
    [Forearm_Duplex_Wrist_19_Bling_Cover_02f.STL]
2023-03-08 Replaced bulk shell with complete shell pair
    The bulk shell can still be used by itself to close the battery compartment in the bulk.
    [Forearm_Duplex_Wrist_19c_TRS_01_Bulk_Cover.STL, Forearm_Duplex_Wrist_19c_TRS_01_Split_Cover.STL]
2023-07-29 The latest Arduino code for the V1.0 Dexhand
    The arduino code for an Arduino Mega 2560 (small footprint).
    This version has 16 standard r/c servos that are controlled by pulse width modulation (pwm) for the fingers and thumb and 3 serial bus servos for the wrist pitch, yaw and roll.
2023-11-15 Schematic of electrical connections
    The electrical connections for the V1.0 DexHand
2023-12-29 Version _10a - Addition of guides for wrist ligament
    To keep the tendon running over the centre of the bearing guides have been added top and bottom.
    The spacing of the guides is 2mm to fit a short length of ptfe tube with a slight flare at each end to help retention.
    [Distal_Wrist_10a_4mm_Holes.STL, Distal_Wrist_10a_5mm_Holes.STL]
2023-12-29 Corrected error
    Clearance for the thumb figure-8 ligament clamp insert was corrected.
    [PLP_THUMB_15b.STL]
2024-01-15 Renamed base joint of thumb parts (CMC_x)
    [CMC_Pitch_15.STL, CMC_Yaw_15.STL]
2024-01-15 Delete Hand_06/CMCa_15.STL
    Replaced with CMC_Pitch_15
    [CMCa_15.STL]
2024-01-15 Delete Hand_06/CMCb_15.STL
    Replaced with CMC_Yaw_15
    [CMCb_15.STL]
2024-01-15 Delete Hand_06/PLP_THUMB_15a.STL
    Replaced with PLP_THUMB_15b.STL
    Corrected insert clearance for the figure-8 ligament clamp.
    [PLP_THUMB_15a.STL]
2024-01-17 Added tendon hanger
    [Thumb_Tendon_Hanger_03a.STL]
2024-01-19 Update to CMC_Yaw
    Updated the CMC_Yaw file with a hole to add the screw for the extension spring.
    [CMC_Yaw_15a.STL]
2024-02-28 Rename Distal_Wrist_10_4mm_Holes.STL to Proximal_Wrist_10_4mm_Holes.STL
    Corrected name.
    [Proximal_Wrist_10_4mm_Holes.STL]
2024-02-28 Rename Distal_Wrist_10a_5mm_Holes.STL to Proximal_Wrist_10a_5mm_Holes.STL
    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
    [Proximal_Wrist_10a_5mm_Holes.STL]
2024-02-28 Rename Distal_Wrist_10a_4mm_Holes.STL to Proximal_Wrist_10a_4mm_Holes.STL
    Corrected name
    [Proximal_Wrist_10a_4mm_Holes.STL]
2024-02-28 Rename Wrist_Proximal_10_Bulk.STL to Wrist_Distal_10_Bulk.STL
    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
    [Wrist_Distal_10_Bulk.STL]
2024-02-28 Rename Wrist_Proximal_10_Split.STL to Wrist_Distal_10_Split.STL
    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
    [Wrist_Distal_10_Split.STL]
2024-02-28 Rename Distal_Wrist_10_Tendon_Hanger_5mm_Holes.STL to Proximal_Wrist_10_Tendon_Hanger_5mm_Holes.STL
    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
    [Proximal_Wrist_10_Tendon_Hanger_5mm_Holes.STL]
2024-02-28 Rename Distal_Wrist_10_Tendon_Hanger_4mm_Holes.STL to Proximal_Wrist_10_Tendon_Hanger_4mm_Holes.STL
    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
    [Proximal_Wrist_10_Tendon_Hanger_4mm_Holes.STL]
2024-02-28 Rename Distal_Wrist_10_Middle.STL to Proximal_Wrist_10_Middle.STL
    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
    [Proximal_Wrist_10_Middle.STL]
2024-03-01 Two minor mods
    To make it easier to fit ligaments through the structure.
    [Forearm_Duplex_Wrist_Bulk_17i.STL]
2024-03-01 Rename Forearm_Duplex_Wrist_Bulk_17i.STL to Forearm_Duplex_Wrist_17i_Bulk.STL
    Matched naming convenion.
    [Forearm_Duplex_Wrist_17i_Bulk.STL]
2024-03-01 Rename folder for forearm pieces
    [Back_of_Hand_23a.STL, Forearm_Duplex_Wrist_17f_Bulk.STL, Forearm_Duplex_Wrist_17i_Bulk.STL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]
2024-03-01 Tidy files
    [Back_of_Hand_23a.STL, Forearm_Duplex_Wrist_19c_Jessie.STL, Forearm_Duplex_Wrist_19c_Jessie_02_Left_Bulk_Cover.STL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]
2024-03-19 Tweak to improve assembly
    Various clearances and minor corrections.
    [Forearm_Duplex_Wrist_17j_Bulk.STL]
2024-03-19 Prints for the wrist pulleys
    The simple pulleys and the centre supports for the wrist pulleys.
    [10_15_4.STL, Wrist_Pulley_Centres_03.STL]
2024-03-19 M3 Socket
    M2 Socket Tool added.
    [M3_Socket_02.STL]
2024-07-26 Added arduino mega code with standard serial connection

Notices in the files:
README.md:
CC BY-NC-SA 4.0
